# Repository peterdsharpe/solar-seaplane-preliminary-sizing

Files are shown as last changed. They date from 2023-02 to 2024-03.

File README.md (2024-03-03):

# Solar Seaplane Conceptual Design

Peter Sharpe

-----

**[UPDATE: See a video of the first flight here!](https://www.youtube.com/watch?v=snPPF-QjMSQ&t=50s)**

This repository contains a conceptual design for a small-scale (13 ft. wingspan) solar-electric seaplane. It was produced as part of my teaching for the class MIT 16.821: Flight Vehicle Development, a senior capstone course that covers aircraft detail design and manufacturing. Using this conceptual design as a point of departure, the students will detail-design and build an airplane aiming to demonstrate net-energy-positive daytime flight and water operations.

A more detailed description is available in [the PowerPoint deck of my kickoff lecture](./Point%20of%20Departure.pptx).

The CONOPS and several features of this airplane are similar to an airplane developed by our seniors during Fall 2022 for our companion course 16.82, which is the "design" half of our class. 

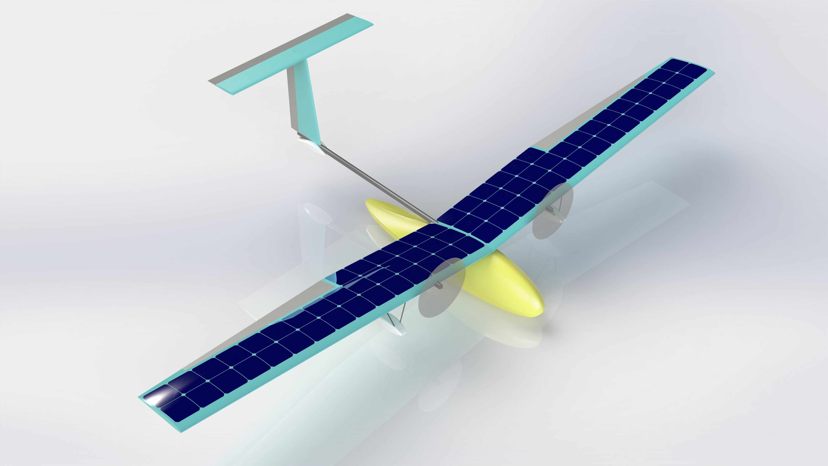
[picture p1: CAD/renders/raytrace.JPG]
raytrace


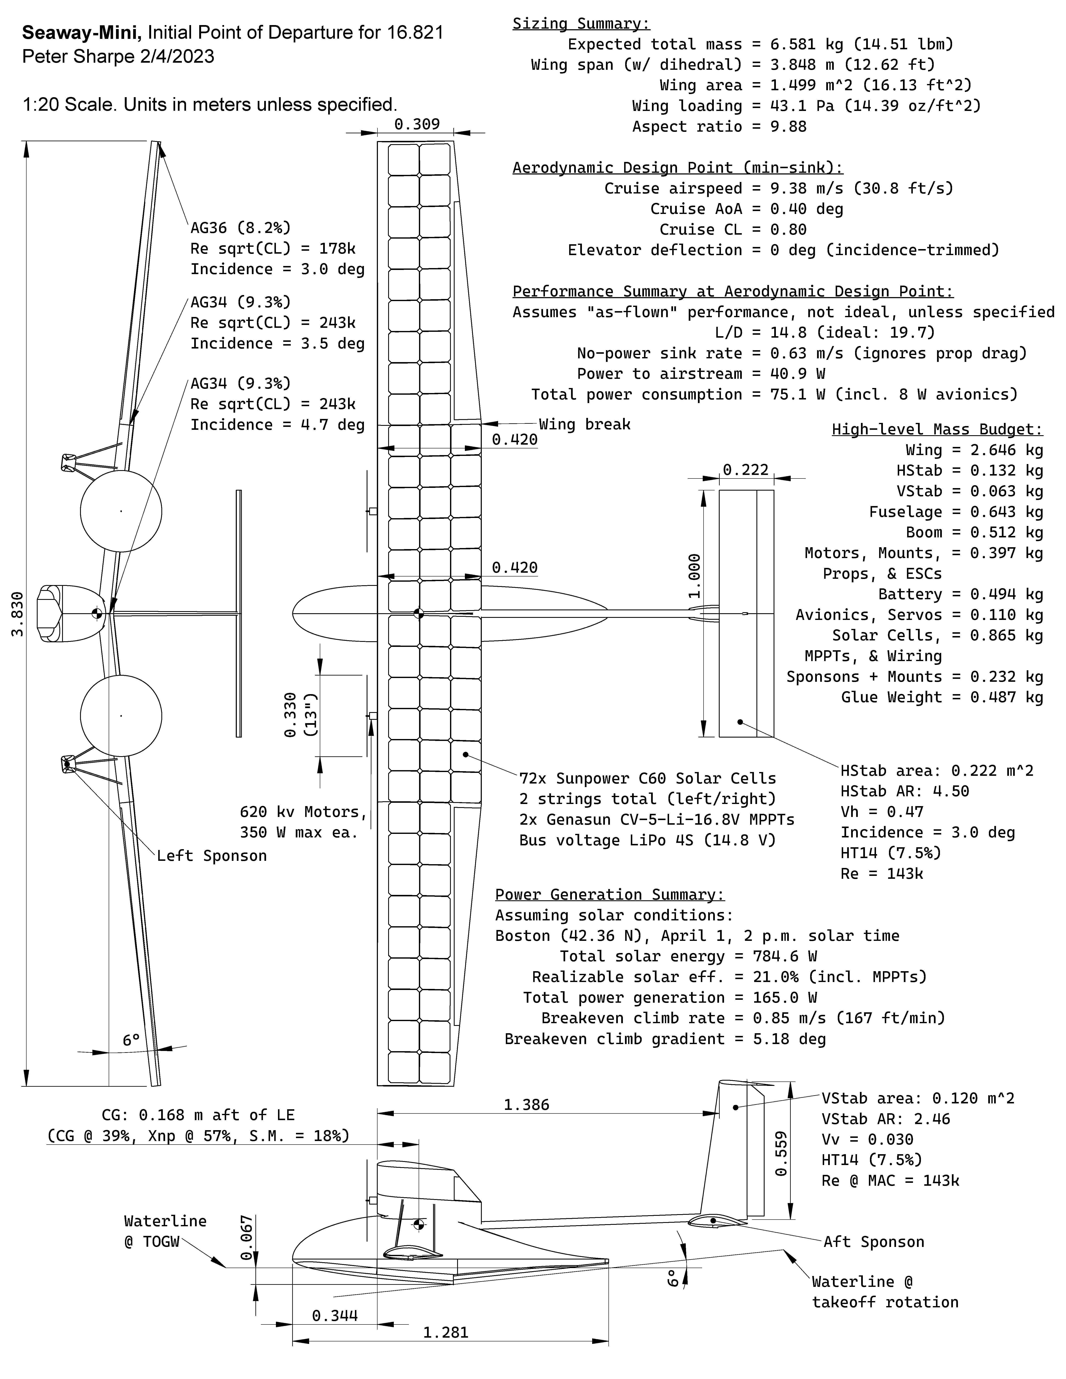
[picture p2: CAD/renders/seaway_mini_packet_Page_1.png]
p1

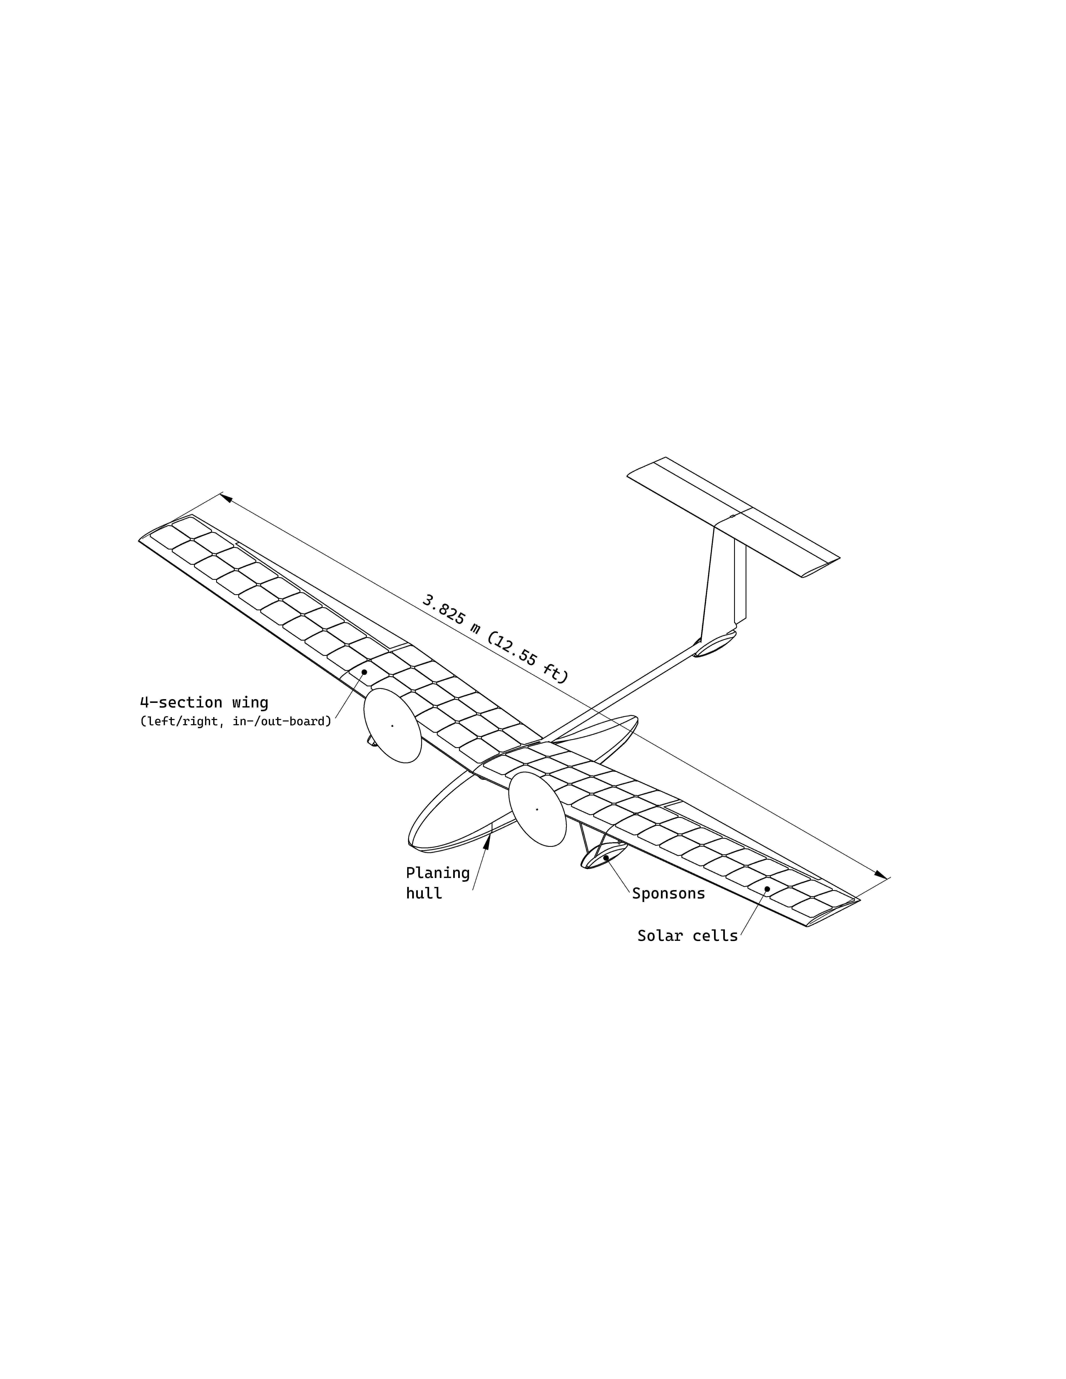
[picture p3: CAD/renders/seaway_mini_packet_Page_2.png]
p2

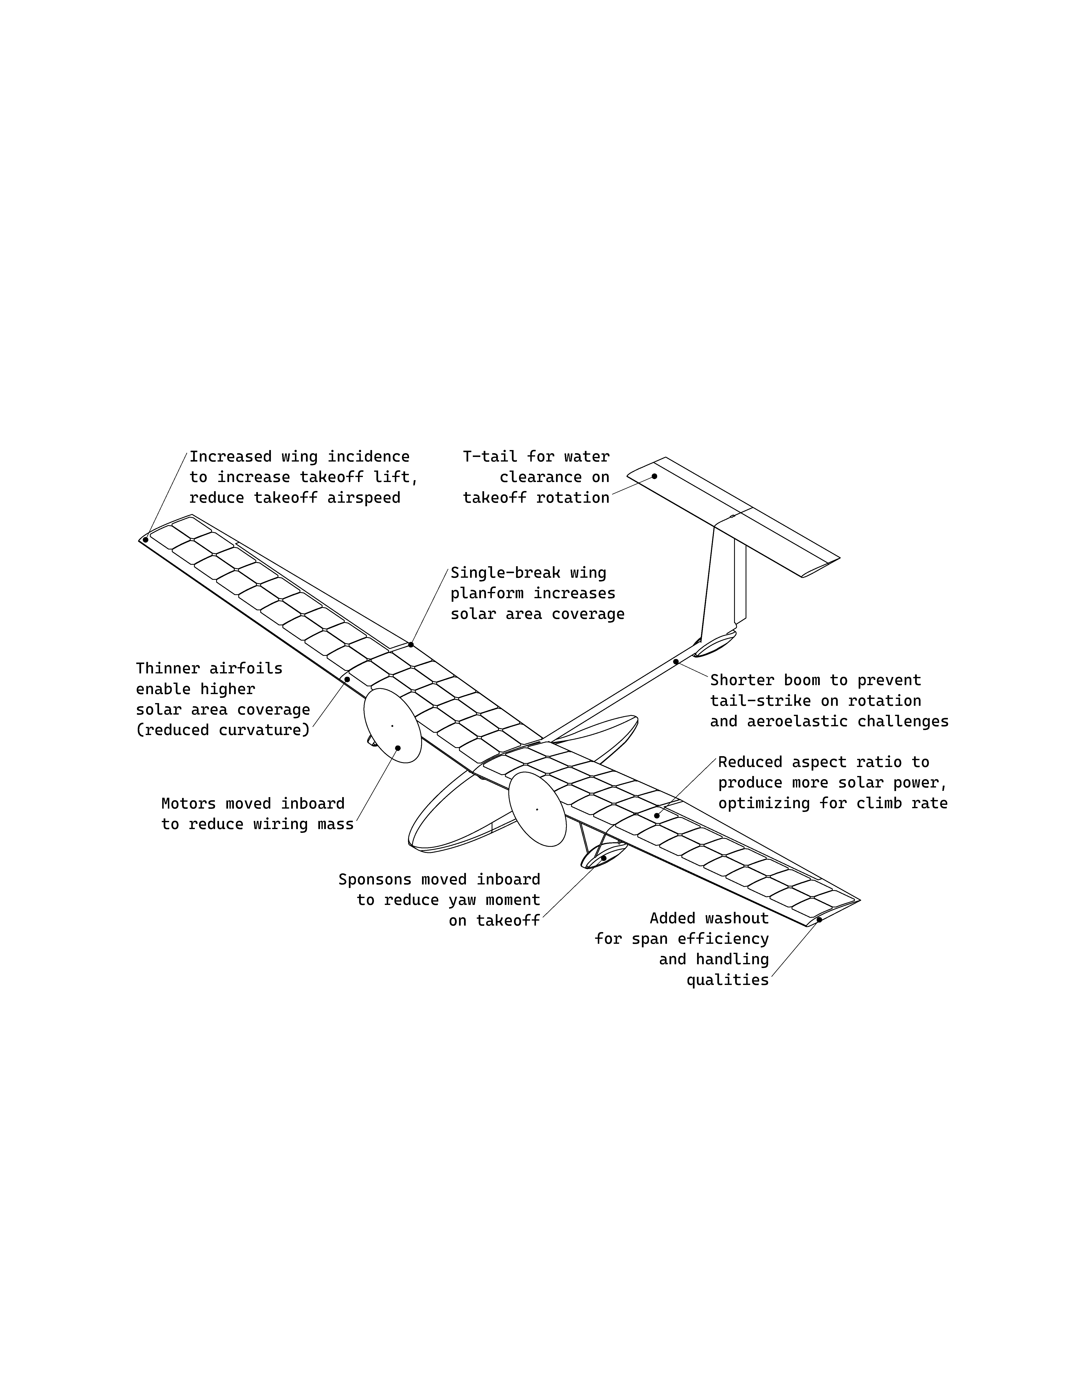
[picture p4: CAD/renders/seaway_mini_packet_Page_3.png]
p3

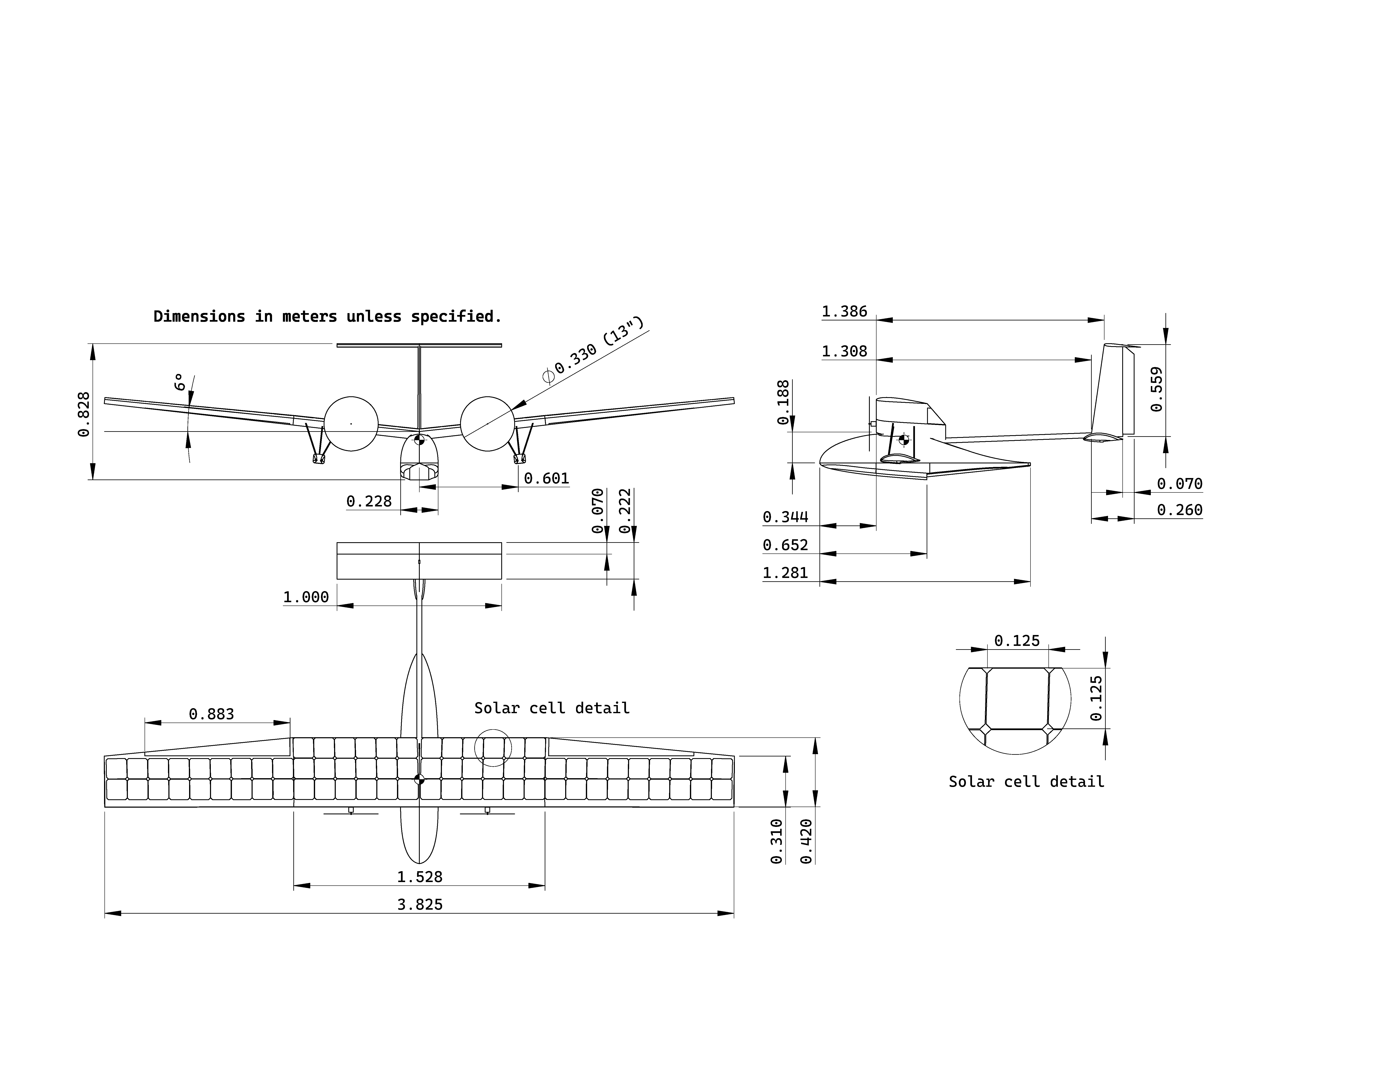
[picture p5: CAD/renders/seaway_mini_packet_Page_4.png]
p4


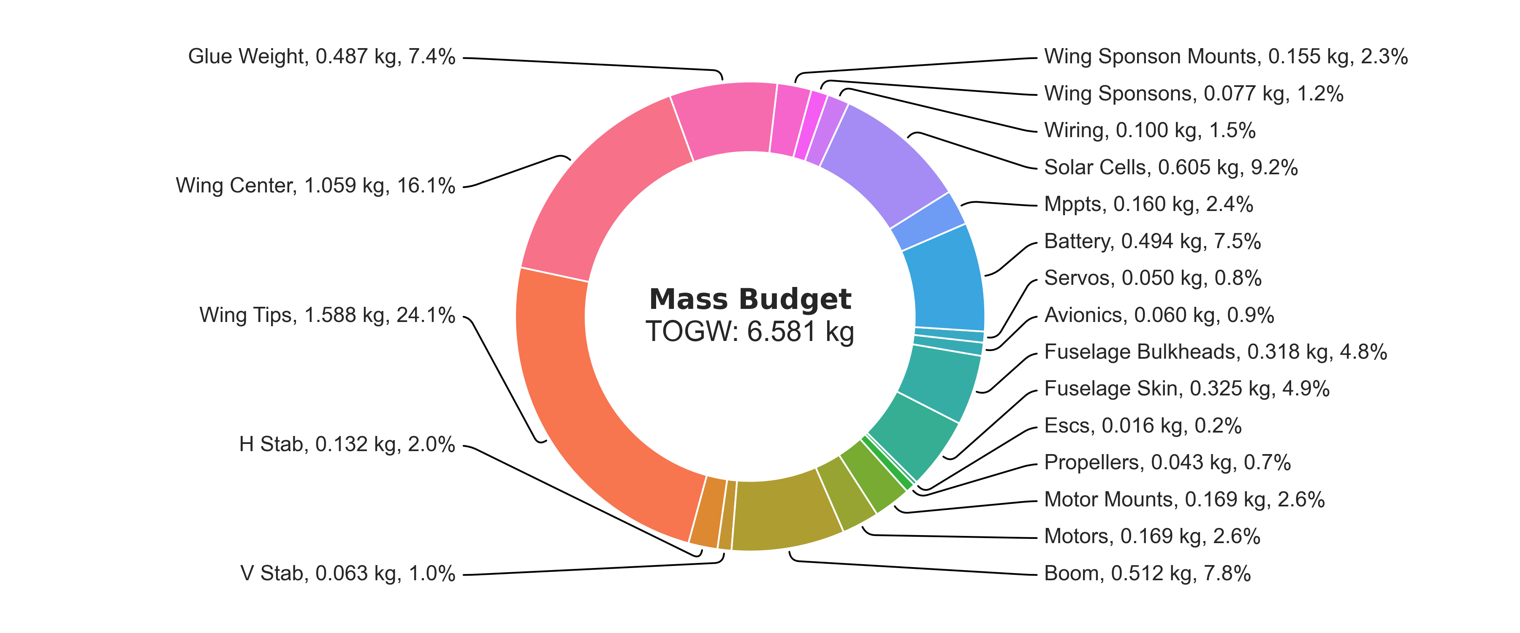
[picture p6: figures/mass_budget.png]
mass


To run:

- Install Python 3.8+, ideally through Anaconda or Miniconda distribution (https://www.anaconda.com/products/distribution)
- In command line, run: `pip install --upgrade aerosandbox[full]` to install all Python package dependencies.
- Run `python design_opt.py` to run the main design optimization code for a point design.
- Run `python span_sweep.py` to run the design space exploration code.

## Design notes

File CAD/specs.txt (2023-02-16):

Sizing Summary:
      Expected total mass = 6.581 kg (14.51 lbm)
                Wing span = 3.848 m (12.62 ft)
                Wing area = 1.499 m^2 (16.13 ft^2)
             Wing loading = 43.1 Pa (14.39 oz/ft^2)

Aerodynamic Design Point (min-sink):
          Cruise airspeed = 9.38 m/s (30.8 ft/s)
               Cruise AoA = 0.40 deg
                Cruise CL = 0.80
      Elevator deflection = 0 deg (trim built-in to incidence)

Performance Summary at Aerodynamic Design Point:
Assumes "as-flown" performance, not ideal, unless specified
                      L/D = 14.8 (ideal: 19.7)
       No-power sink rate = 0.63 m/s (ignores prop drag)
       Power to airstream = 40.9 W
  Total power consumption = 75.1 W

Power Generation Summary:
Solar conditions: Boston (42.36 N), April 1, 2 p.m. solar time
       Total solar energy = 784.6 W
    Realizable solar eff. = 21.0% (includes MPPTs)
   Total power generation = 165.0 W

For net-zero energy:
		Climb rate = 0.62 m/s (122 ft/min)
        Climb gradient = 3.45 deg

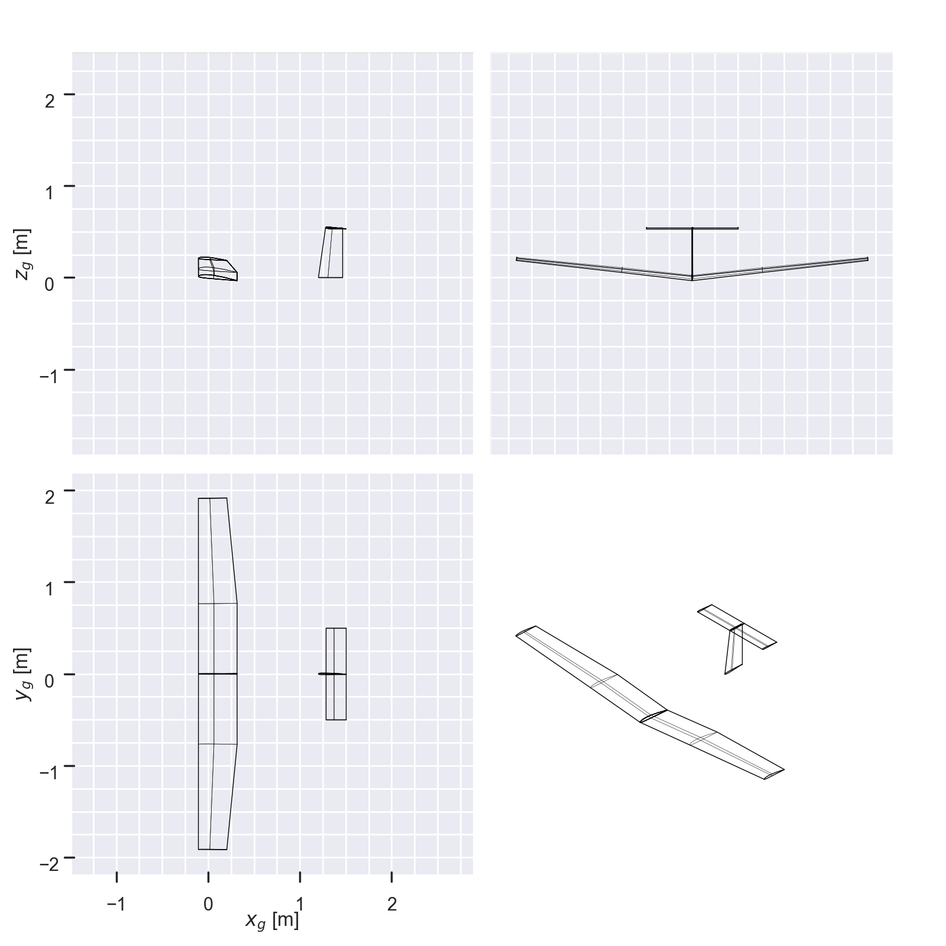
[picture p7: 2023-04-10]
figures/three_view.png

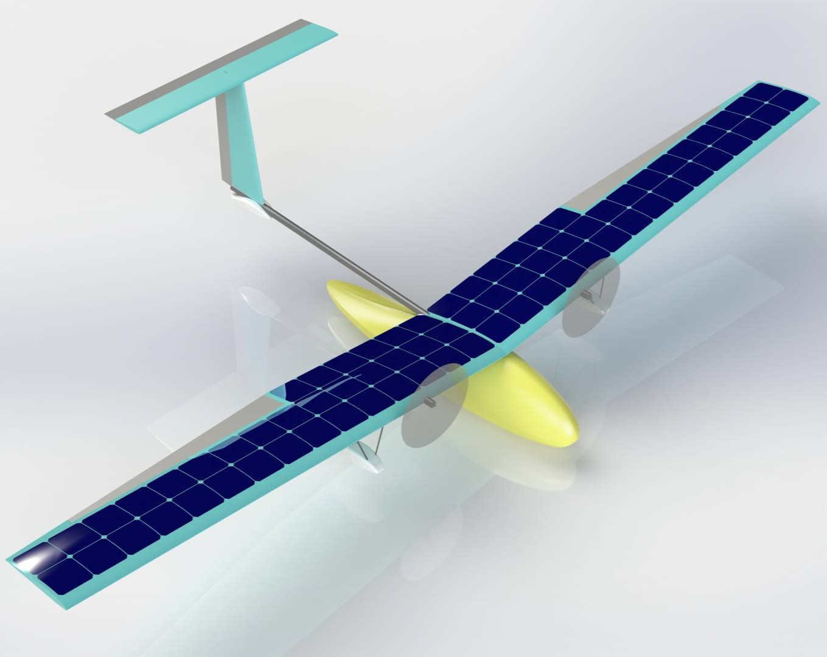
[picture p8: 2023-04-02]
CAD/renders/raytrace-lowres.jpg

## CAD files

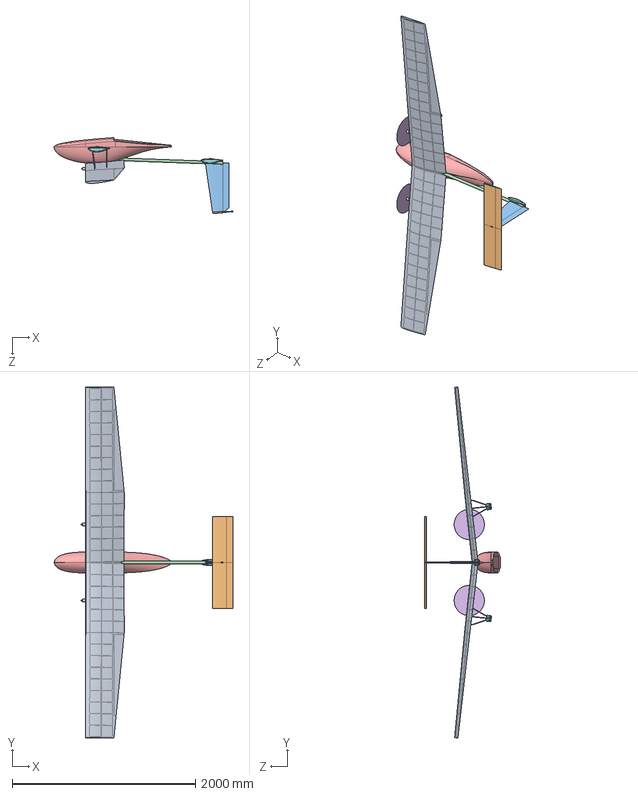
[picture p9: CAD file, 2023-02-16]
CAD/seaway_mini.SLDASM
1951.0 x 3830.3 x 827.7 mm
Wing
HStab
VStab
Boom^seaway_mini
pod_only
Propeller^seaway_mini x 2
Motor x 2
Sponson Placeholder x 3
Inboard Sponson Mount^seaway_mini x 2
Outboard Sponson Mount^seaway_mini x 2
Aft Sponson Mount^seaway_mini x 2

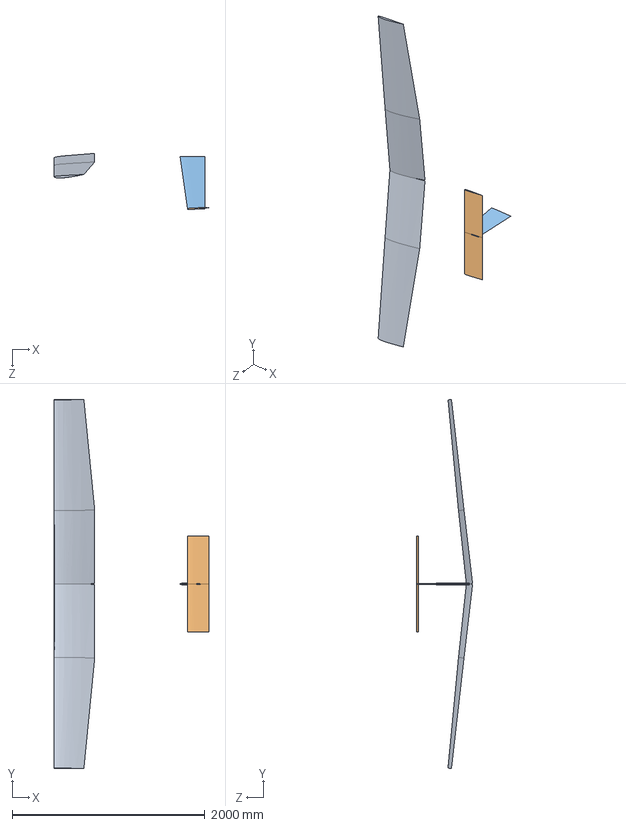
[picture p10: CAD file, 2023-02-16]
CAD/seaway_mini_lifting_surfaces_from_asb_converted.SLDASM
1607.5 x 3830.3 x 584.0 mm

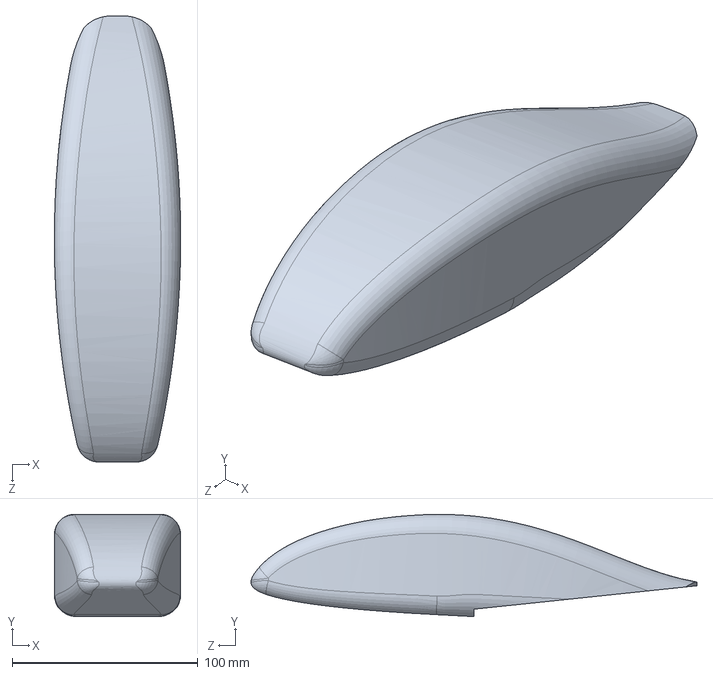
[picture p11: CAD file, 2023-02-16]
CAD/Sponson Placeholder.SLDPRT
68.0 x 55.0 x 240.0 mm

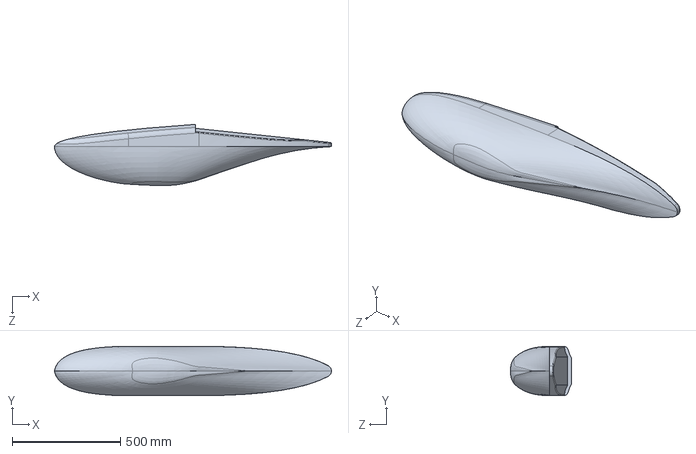
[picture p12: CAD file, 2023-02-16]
CAD/pod_only.SLDPRT
1280.8 x 228.1 x 283.3 mm

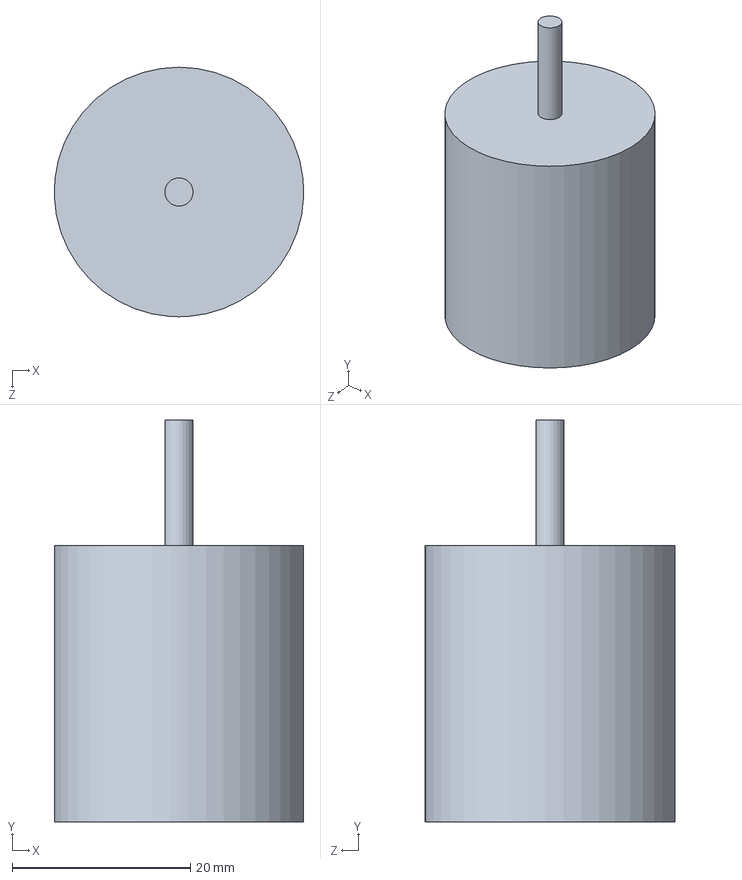
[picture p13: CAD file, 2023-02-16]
CAD/Motor.SLDPRT
28.0 x 45.1 x 28.0 mm

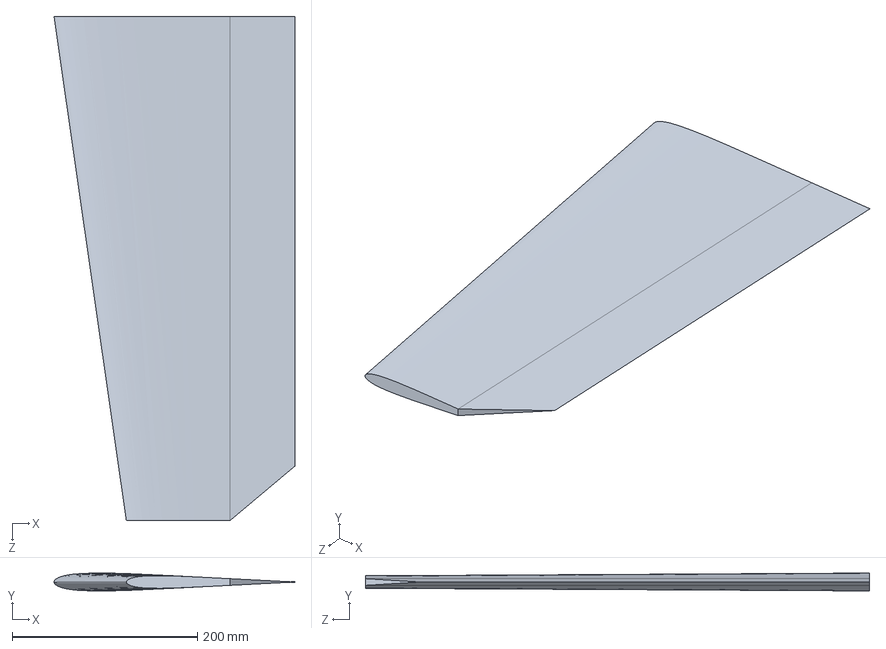
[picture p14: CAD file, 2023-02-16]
CAD/VStab.SLDPRT
260.0 x 19.3 x 543.9 mm

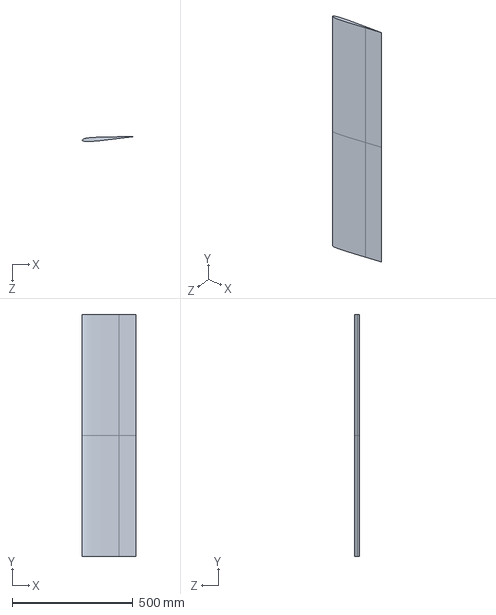
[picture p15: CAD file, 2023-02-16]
CAD/HStab.SLDPRT
221.8 x 1000.5 x 21.5 mm

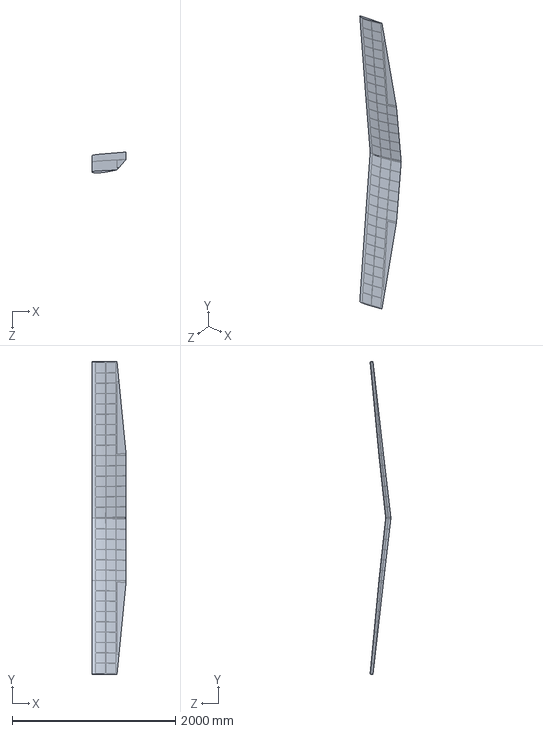
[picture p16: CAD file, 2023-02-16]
CAD/Wing.SLDPRT
422.1 x 3830.3 x 256.9 mm

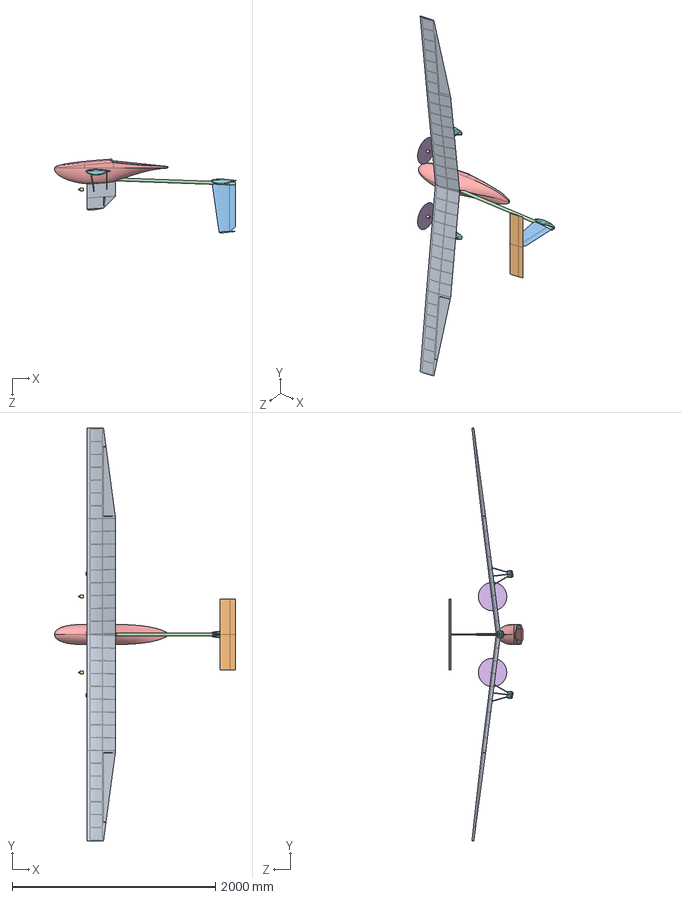
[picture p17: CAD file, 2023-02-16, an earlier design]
old_CAD/seaway_mini_CAD_v2/seaway_mini.SLDASM
1783.3 x 4061.1 x 727.0 mm
Wing
HStab
VStab
Boom^seaway_mini
pod_only
Propeller^seaway_mini x 2
Propdrive v2 2830 800 kv Motor x 2
Sponson Placeholder x 3
Inboard Sponson Mount^seaway_mini x 2
Outboard Sponson Mount^seaway_mini x 2
Aft Sponson Mount^seaway_mini x 2

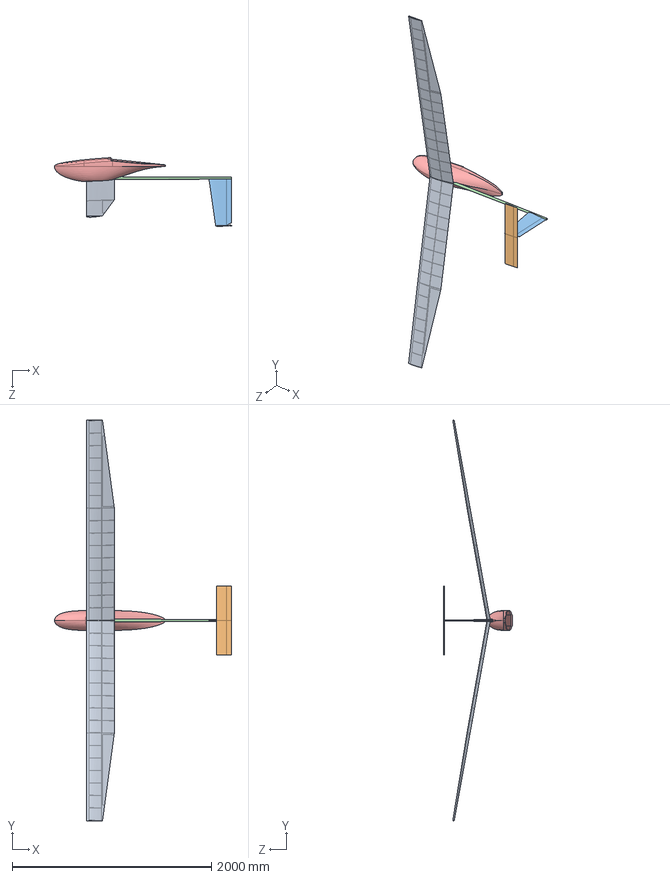
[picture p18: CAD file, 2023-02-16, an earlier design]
old_CAD/seaway_mini_CAD_v1/seaway_mini.SLDASM
1781.7 x 4028.2 x 692.9 mm
Wing^seaway_mini
HStab^seaway_mini
VStab^seaway_mini
Boom^seaway_mini
pod_only

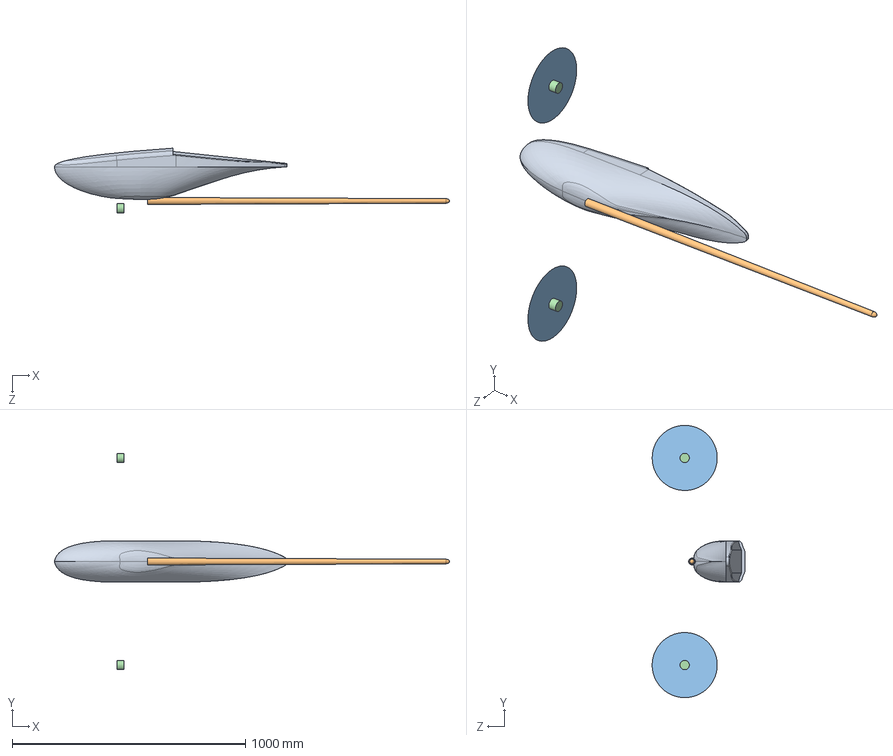
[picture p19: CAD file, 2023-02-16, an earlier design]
old_CAD/seaway_mini_CAD_v0/seaway_mini.SLDASM
1695.2 x 1168.3 x 397.8 mm
Pod Only
Boom^seaway_mini
Props^seaway_mini
Motors^seaway_mini

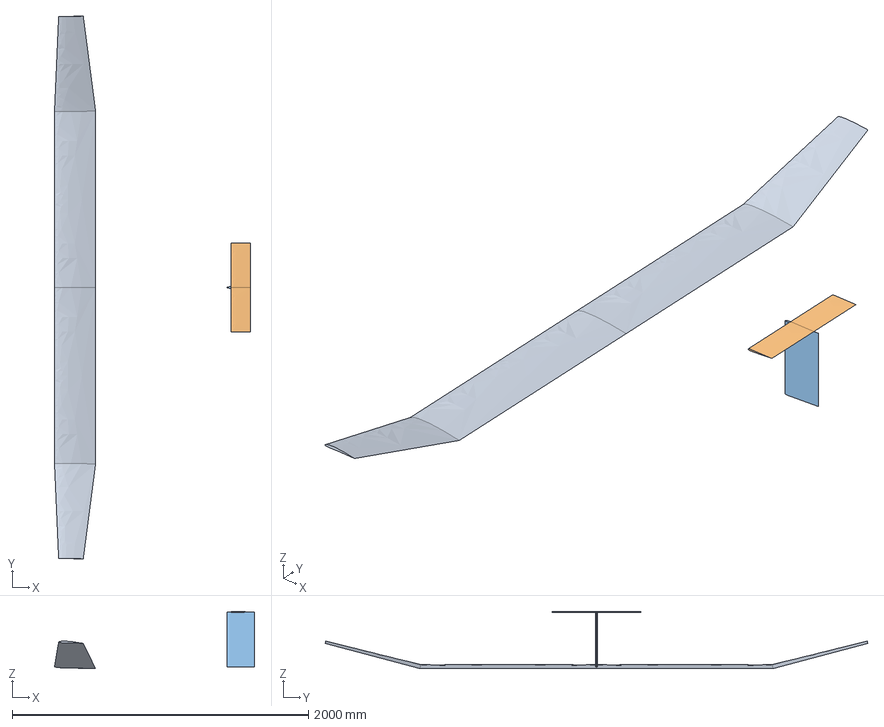
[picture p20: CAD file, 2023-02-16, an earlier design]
old_CAD/seaway_mini_CAD_v0/seaway_mini_lifting_surfaces.step
1349.5 x 3662.0 x 386.6 mm

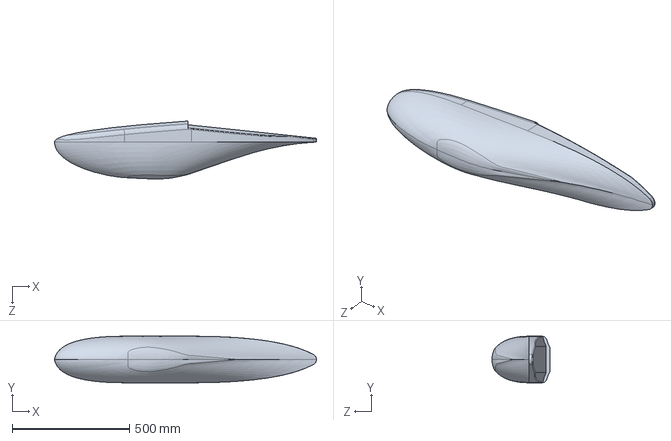
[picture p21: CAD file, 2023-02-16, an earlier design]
old_CAD/seaway_mini_CAD_v1/pod_only.SLDPRT
1116.5 x 198.8 x 247.0 mm

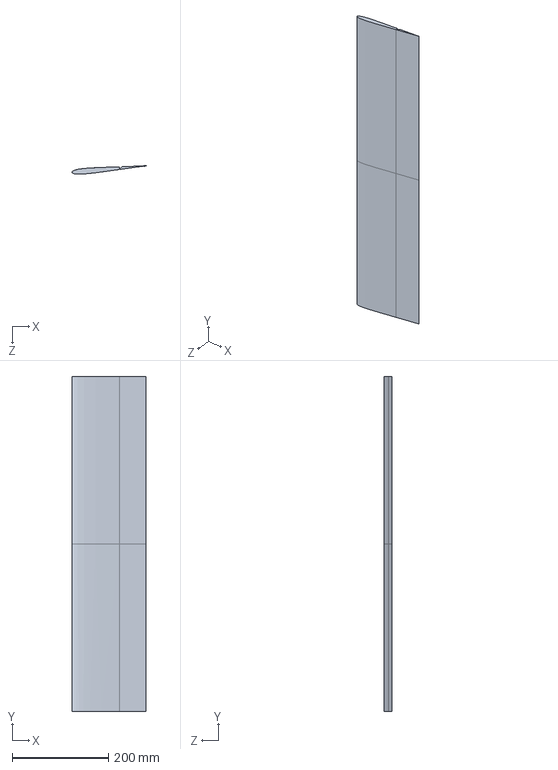
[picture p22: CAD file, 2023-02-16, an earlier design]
old_CAD/seaway_mini_CAD_v2/HStab.SLDPRT
154.0 x 695.6 x 17.4 mm

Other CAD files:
CAD/seaway_mini_lifting_surfaces_from_asb.step
old_CAD/seaway_mini_CAD_v0/Pod Only.SLDPRT
old_CAD/seaway_mini_CAD_v1/seaway_mini_lifting_surfaces_from_asb.step
old_CAD/seaway_mini_CAD_v0/airplane.step
CAD/hstab.IGS
CAD/seaway_mini.SLDDRW
CAD/seaway_mini.x_t
CAD/vstab.IGS
CAD/wing.IGS
old_CAD/seaway_mini_CAD_v0/Original OML.SLDPRT
old_CAD/seaway_mini_CAD_v0/seaway_mini_lifting_surfaces.SLDASM
old_CAD/seaway_mini_CAD_v2/Sponson Placeholder.SLDPRT
old_CAD/seaway_mini_CAD_v2/VStab.SLDPRT
old_CAD/seaway_mini_CAD_v2/Wing.SLDPRT
old_CAD/seaway_mini_CAD_v2/pod_only.SLDPRT
old_CAD/seaway_mini_CAD_v2/seaway_mini.SLDDRW
old_CAD/seaway_mini_CAD_v2/seaway_mini_lifting_surfaces_from_asb.step

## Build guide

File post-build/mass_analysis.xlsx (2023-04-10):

Component | Mass @ Initial Conceptual Design [kg] | Mass @ Detailed Design (4/8/23) [kg] | Notes | Ratio | Analysis of Deviation
wing | 2.647 | 2.990 |  | 1.13
h_stab | 0.132 | 0.215 |  | 1.63
v_stab | 0.063 | 0.145 |  | 2.30
boom | 0.512 | 0.504 |  | 0.98
motors | 0.169 | 0.354 |  | 2.09 | Not an issue; purchased motors were over-sized
motor_mounts | 0.169 | 0.248 |  | 1.47 | Not an issue; overbuilt
propellers | 0.043 | 0.080 |  | 1.86 | Used bad propeller model - should validate this
ESCs | 0.016 | 0.066 |  | 4.12
fuselage_skin | 0.325 | 0.316 |  | 0.97
fuselage_bulkheads | 0.318 | 0.105 |  | 0.33
avionics | 0.060 | unknown |  | #VALUE!
servos | 0.050 | 0.114 |  | 2.28
battery | 0.494 | 0.394 |  | 0.80
MPPTs | 0.160 | 0.040 | no cases | 0.25
solar_cells | 0.605 | 0.652 | Includes dogbones | 1.08
wiring | 0.100 | unknown |  | #VALUE!
wing_sponsons | 0.077 | 0.300 | guess | 3.90
wing_sponson_mounts | 0.155 | 0.025 |  | 0.16
glue_weight | 0.487 |  |  | 0.00
BEC for servos |  | 0.020 |  | #DIV/0!
fuselage floor |  | 0.125 |  | #DIV/0!
fuselage truss |  | 0.250 |  | #DIV/0!
avionics box |  | 0.050 |  | #DIV/0!
control horns |  | 0.025 |  | #DIV/0!
pitot probe |  | 0.050 |  | #DIV/0!
Total | 6.582 | 7.068

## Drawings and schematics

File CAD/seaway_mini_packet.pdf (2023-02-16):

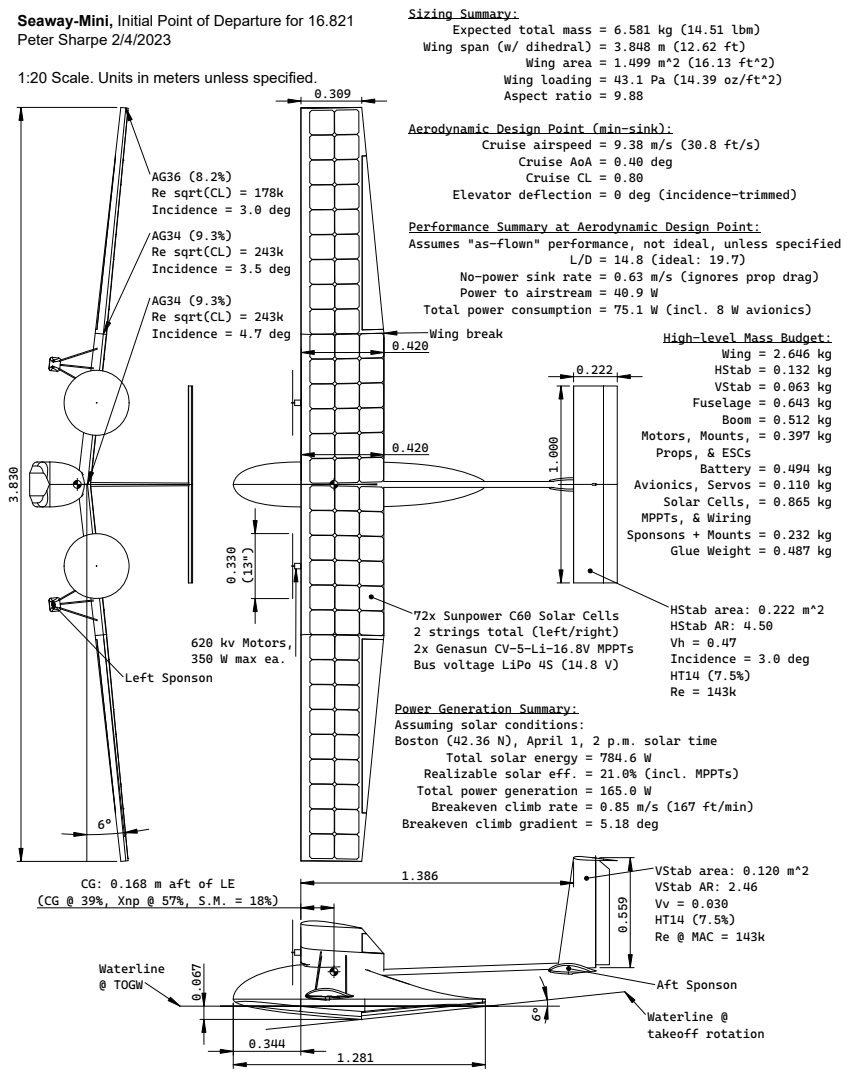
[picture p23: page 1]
Sizing Summary:; L/D = 14.8 (ideal: 19.7); Wing = 2.646 kg HStab = 0.132 kg VStab = 0.063 kg Fuselage = 0.643 kg Boom = 0.512 kg; Battery = 0.494 kg; Left Sponson; VStab area: 0.120 m^2 VStab AR: 2.46 Vv = 0.030 HT14 (7.5%) Re @ MAC = 143k; Waterline @ TOGW; Waterline @ takeoff rotation; Aft Sponson; (CG @ 39%, Xnp @ 57%, S.M. = 18%); HStab area: 0.222 m^2 HStab AR: 4.50 Vh = 0.47 Incidence = 3.0 deg HT14 (7.5%) Re = 143k; 620 kv Motors, 350 W max ea.

Seaway-Mini, Initial Point of Departure for 16.821
Peter Sharpe 2/4/2023

Expected total mass = 6.581 kg (14.51 lbm)
Wing span (w/ dihedral) = 3.848 m (12.62 ft)

Wing area = 1.499 m^2 (16.13 ft^2)
Wing loading = 43.1 Pa (14.39 oz/ft^2)
Aspect ratio = 9.88

1:20 Scale. Units in meters unless specified.

Aerodynamic Design Point (min-sink):

Cruise airspeed = 9.38 m/s (30.8 ft/s)
Cruise AoA = 0.40 deg
Cruise CL = 0.80

Re sqrt(CL) = 178k
Incidence = 3.0 deg
Re sqrt(CL) = 243k
Incidence = 3.5 deg

Elevator deflection = 0 deg (incidence-trimmed)

Performance Summary at Aerodynamic Design Point:
Assumes "as-flown" performance, not ideal, unless specified

No-power sink rate = 0.63 m/s (ignores prop drag)
Power to airstream = 40.9 W
Total power consumption = 75.1 W (incl. 8 W avionics)
Wing break

Incidence = 4.7 deg

High-level Mass Budget:

Motors, Mounts, = 0.397 kg
Props, & ESCs

Avionics, Servos = 0.110 kg
Solar Cells, = 0.865 kg
MPPTs, & Wiring
Sponsons + Mounts = 0.232 kg

Glue Weight = 0.487 kg

72x Sunpower C60 Solar Cells
2 strings total (left/right)
2x Genasun CV-5-Li-16.8V MPPTs
Bus voltage LiPo 4S (14.8 V)

Power Generation Summary:
Assuming solar conditions:
Boston (42.36 N), April 1, 2 p.m. solar time

Total solar energy = 784.6 W
Realizable solar eff. = 21.0% (incl. MPPTs)
Total power generation = 165.0 W
Breakeven climb rate = 0.85 m/s (167 ft/min)
Breakeven climb gradient = 5.18 deg

CG: 0.168 m aft of LE

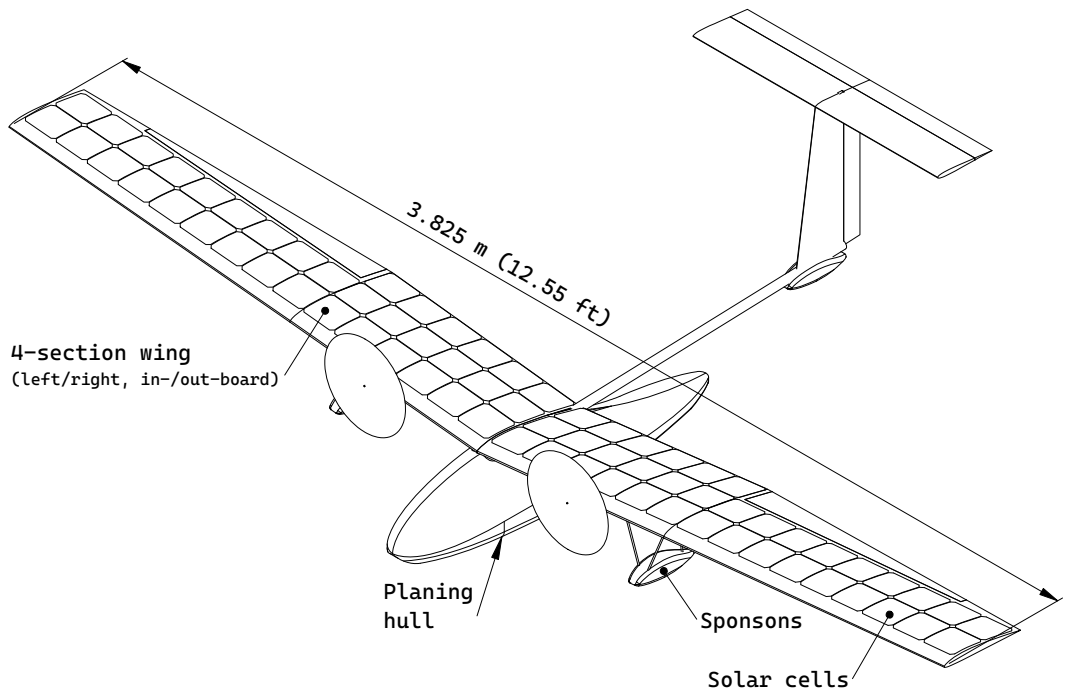
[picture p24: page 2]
Solar cells; Sponsons; Planing hull

4-section wing
(left/right, in-/out-board)

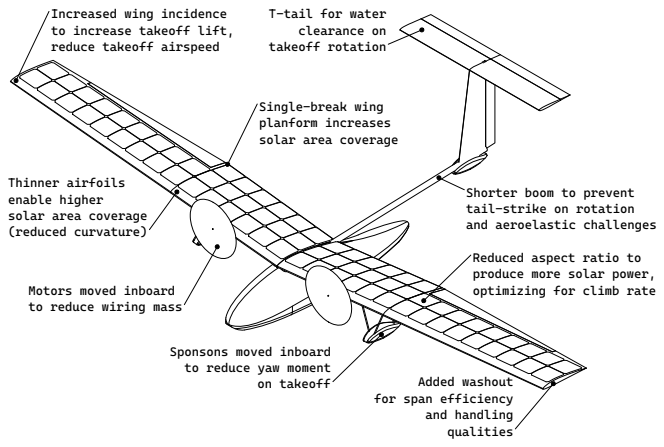
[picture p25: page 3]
on takeoff; Added washout; and handling qualities

Increased wing incidence
to increase takeoff lift,
reduce takeoff airspeed

T-tail for water
clearance on
takeoff rotation

Single-break wing
planform increases
solar area coverage

Thinner airfoils
enable higher
(reduced curvature)

Shorter boom to prevent
tail-strike on rotation
and aeroelastic challenges

Reduced aspect ratio to
produce more solar power,
optimizing for climb rate

Motors moved inboard
to reduce wiring mass

Sponsons moved inboard
to reduce yaw moment

for span efficiency

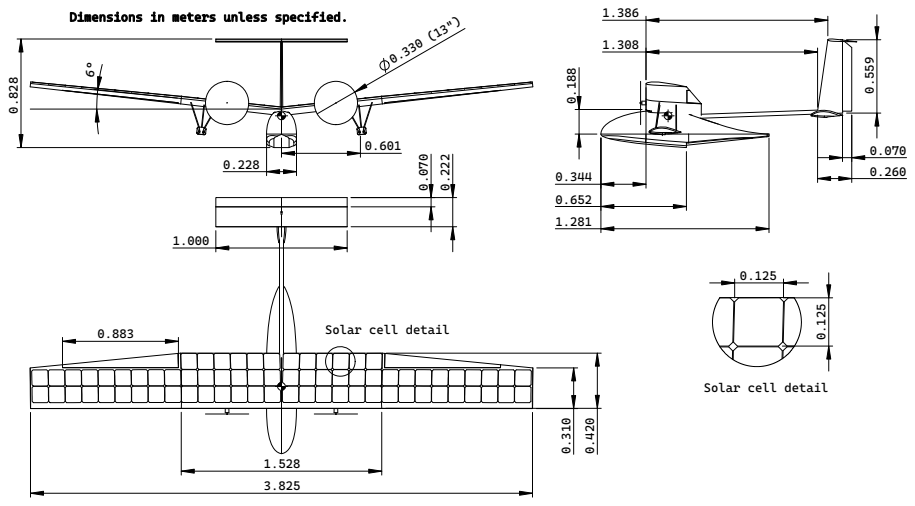
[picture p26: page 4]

Dimensions in meters unless specified.

Solar cell detail 0.883

Solar cell detail

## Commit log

2023-02-16 add ignore
    [HStab.SLDPRT, Motor.SLDPRT, Original OML.SLDPRT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]
2023-04-10 modernizing syntax, add post-build numbers
    [mass_analysis.xlsx]
